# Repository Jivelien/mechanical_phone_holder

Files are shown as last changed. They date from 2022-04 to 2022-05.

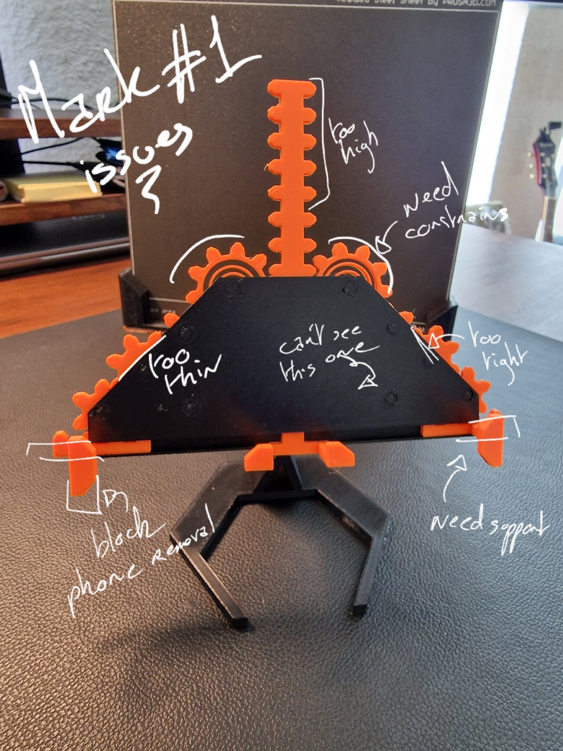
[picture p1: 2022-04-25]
issues_tracing.jpg

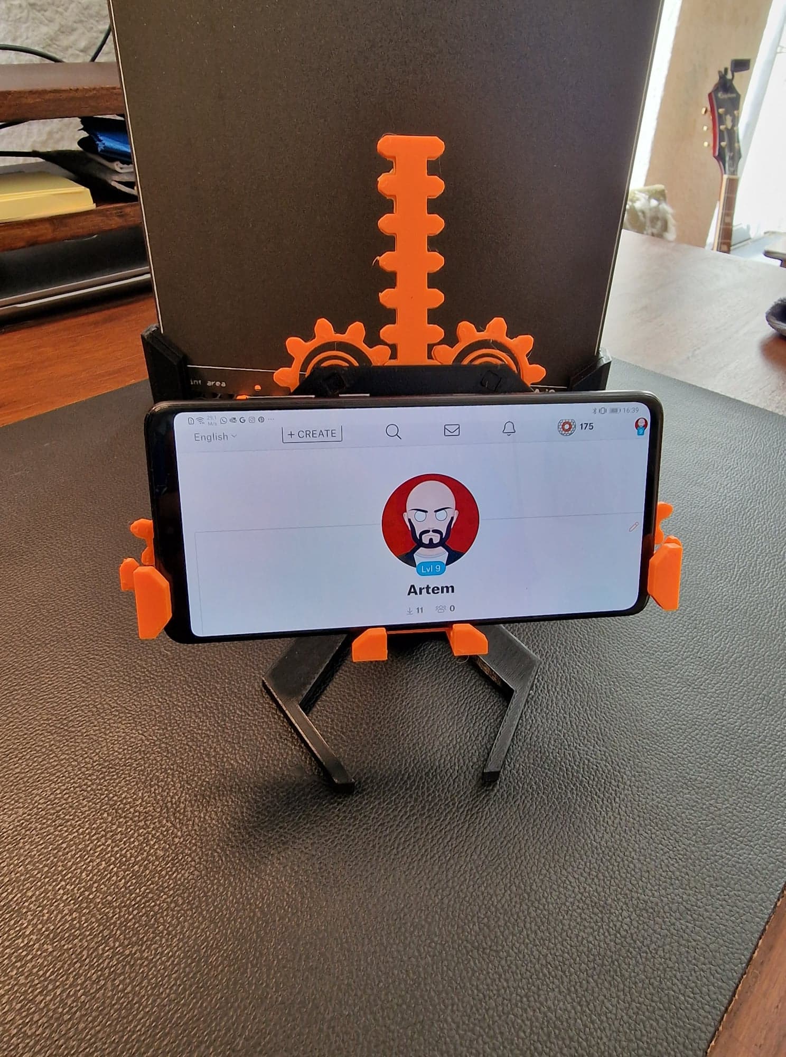
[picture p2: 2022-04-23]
220422-printableSubmission/mk1_horizontal_w_phone.jpg

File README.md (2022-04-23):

# Mechanical phone stand -  Mk 1

This phone gear was design with the constrain to move only using gears (and racks).

This phone holder is suitable for a phone with max dimension of 90x190x19 (a really big phone), and minimal of 60x40x__ (a tamagochi… ¯\_(ツ)_/¯)

When you put your phone on the stand, the vertical rack will move down and leads to all gear moving and grabing your phone from each side.

The top gears contains a spring, which mean that when you take off your phone, it will automatically come back to its default position.

All the design was compute using OpenScad using an homemade gears generator library.

I've learn a lot making this project, and I hope you like it!
Happy printing !

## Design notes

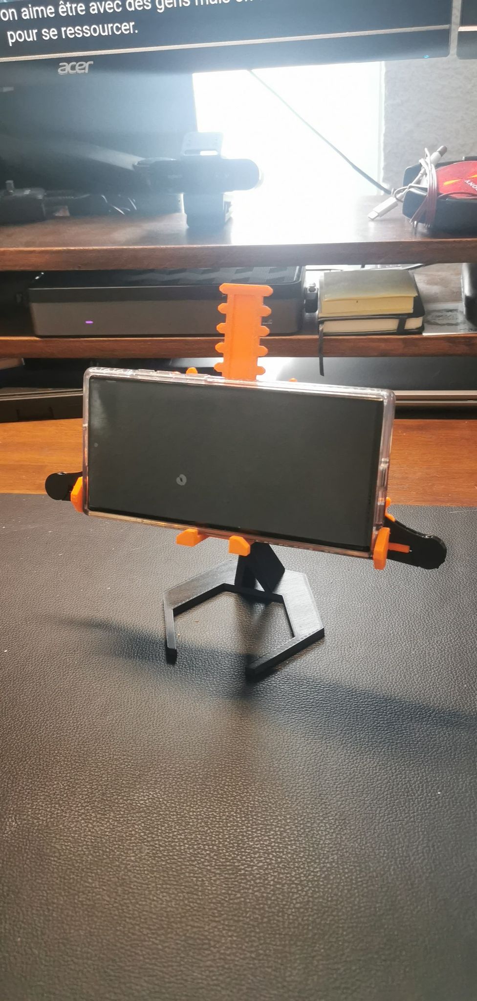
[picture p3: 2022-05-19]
20220519-Mk2_Publish/280579185_324572459750847_7880518313641460600_n.jpg

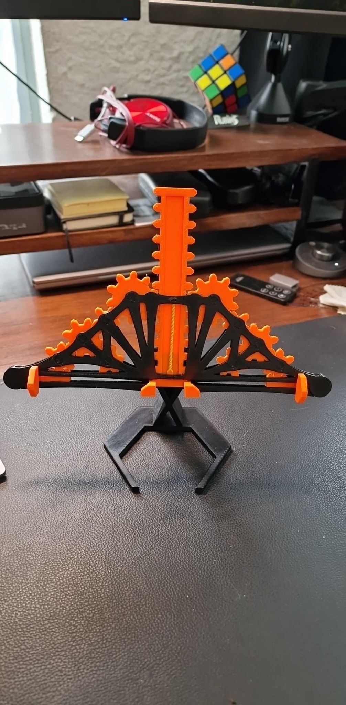
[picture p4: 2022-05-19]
20220519-Mk2_Publish/281888711_434815515040241_3250742157388597709_n.jpg

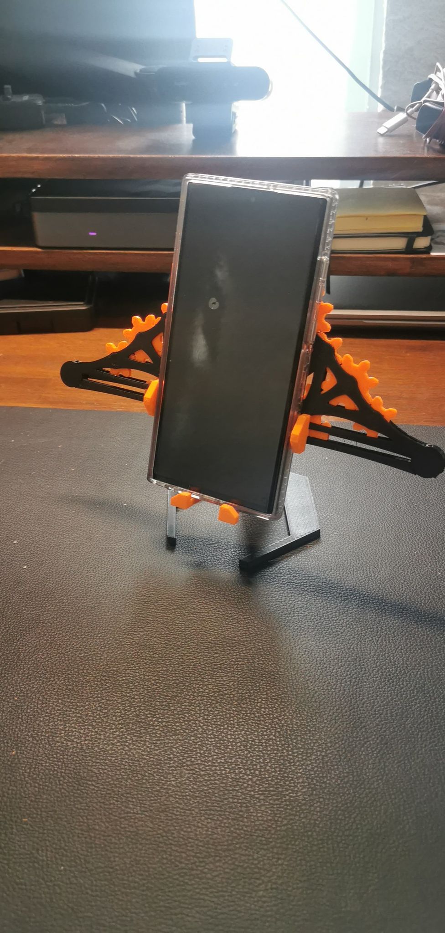
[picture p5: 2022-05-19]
20220519-Mk2_Publish/280890000_410508580699683_3673960678102073021_n.jpg

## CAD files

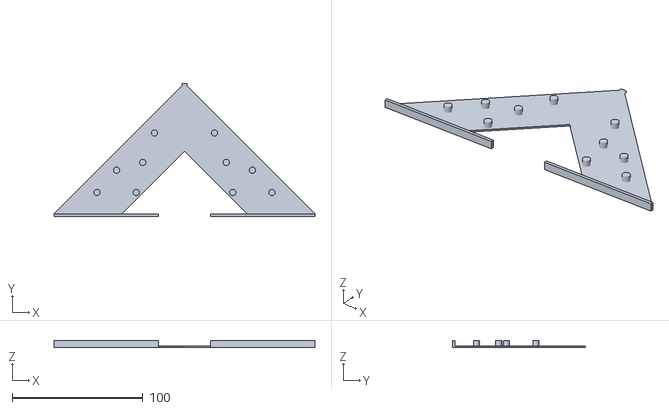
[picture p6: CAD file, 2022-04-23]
20220413-printedPoc/support.stl
200.0 x 102.0 x 5.00

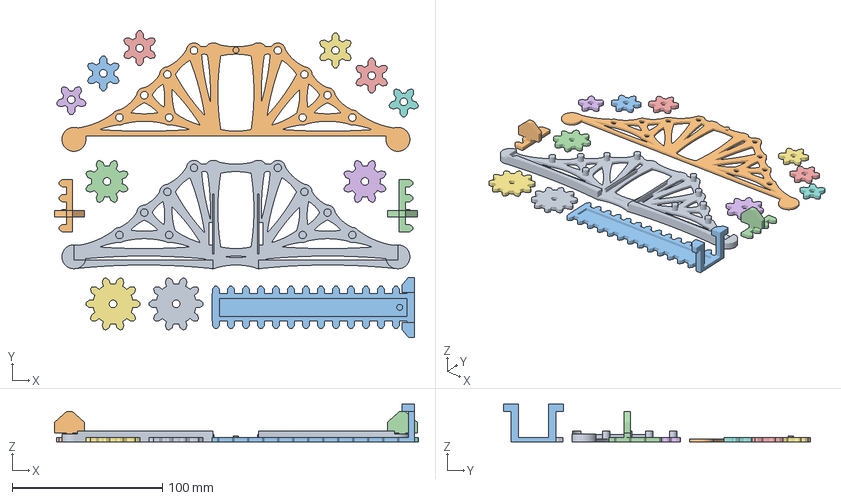
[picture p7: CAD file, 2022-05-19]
20220519-Mk2_Publish/bottom.3mf
242.7 x 204.5 x 25.0 mm
bottom.stl
top.stl
system.stl_1
system.stl_2
system.stl_3
system.stl_4
system.stl_5
system.stl_6
system.stl_7
system.stl_8
system.stl_9
system.stl_10
system.stl_11
system.stl_12
system.stl_13

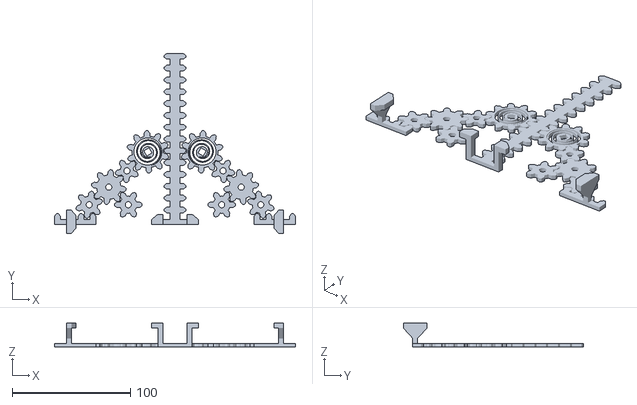
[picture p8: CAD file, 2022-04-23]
220422-printableSubmission/mk1_gears.stl
204.0 x 152.6 x 20.0

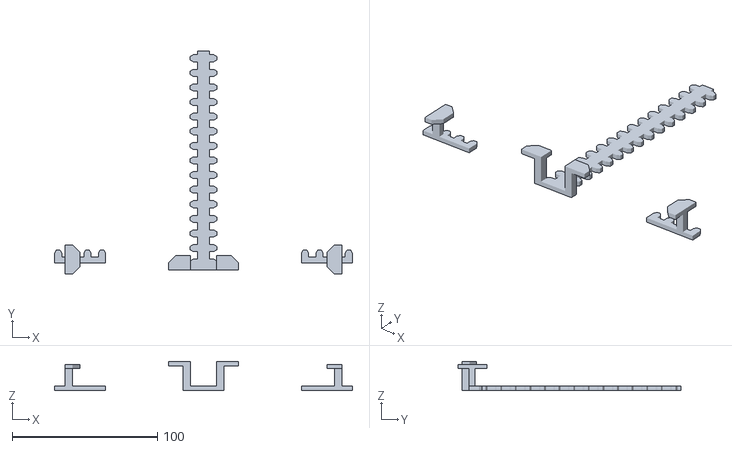
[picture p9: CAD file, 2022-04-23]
20220413-printedPoc/rack.stl
205.1 x 153.5 x 20.0

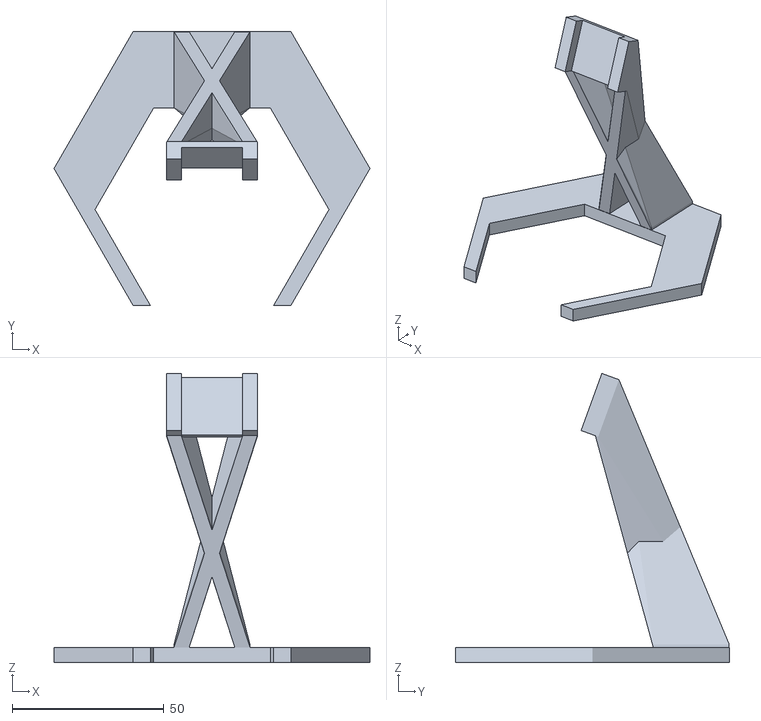
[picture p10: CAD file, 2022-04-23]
220422-printableSubmission/mk1_foot.stl
104.0 x 90.1 x 95.2

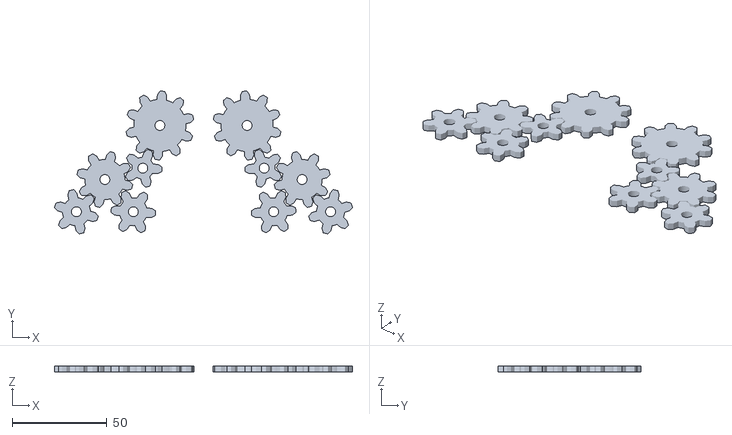
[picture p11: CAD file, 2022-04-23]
20220413-printedPoc/gear.stl
157.1 x 75.3 x 3.00

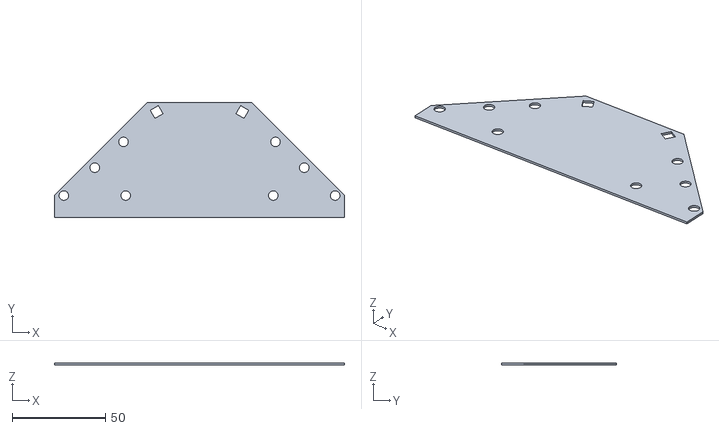
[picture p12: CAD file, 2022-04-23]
220422-printableSubmission/mk1_top_cover.stl
155.2 x 61.4 x 1.00

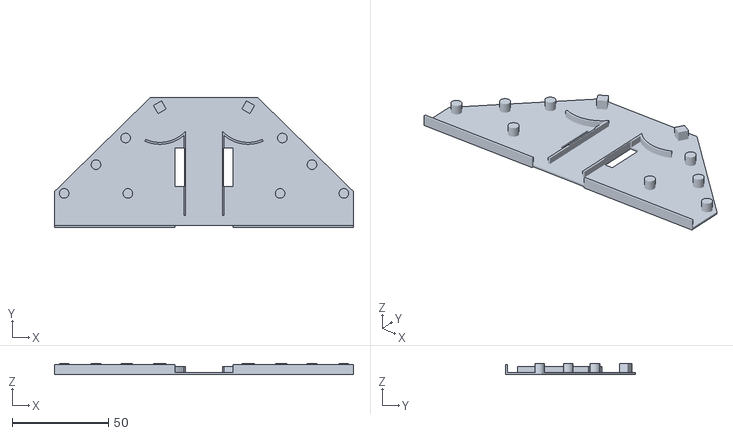
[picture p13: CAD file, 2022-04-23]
220422-printableSubmission/mk1_back.stl
155.2 x 67.4 x 5.50

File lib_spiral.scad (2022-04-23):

module line(point1, point2, width = 1, cap_round = true) {
    angle = 90 - atan((point2[1] - point1[1]) / (point2[0] - point1[0]));
    offset_x = 0.5 * width * cos(angle);
    offset_y = 0.5 * width * sin(angle);

    offset1 = [-offset_x, offset_y];
    offset2 = [offset_x, -offset_y];

    if(cap_round) {
        translate(point1) circle(d = width, $fn = 24);
        translate(point2) circle(d = width, $fn = 24);
    }

    polygon(points=[
        point1 + offset1, point2 + offset1,  
        point2 + offset2, point1 + offset2
    ]);
}

module polyline(points, width = 1) {
    module polyline_inner(points, index) {
        if(index < len(points)) {
            line(points[index - 1], points[index], width);
            polyline_inner(points, index + 1);
        }
    }

    polyline_inner(points, 1);
}

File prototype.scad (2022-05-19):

include <libp_gear.scad>
include <lib_spiral.scad>
include <libp_branch.scad>

toothThickness=5;
toothHeight=5;
thickness =3;
tolerance=0.1;
pin_diameter = 5;
donut_thickness = 0;
hole_diameter = pin_diameter + tolerance;

gear1_numberOfTeeth = 6;
gear2_numberOfTeeth = 8;
gear3_numberOfTeeth = 6;
gear4_numberOfTeeth = 5;
gear5_numberOfTeeth = 10;

centralRack_numberOfTeeth = 14;
sideRack_numberOfTeeth = 4;
sideRackHeight=7;
centralRackHeight=12;
sideRack_translate=11.2;

top_thickness=2;
branch_diameter=5;


pin_height= donut_thickness*2 + top_thickness*2 + tolerance *2 + thickness;

angle_1_2 = 42;
angle_2_3 = -angle_1_2;
angle_2_4 = 180-angle_1_2;
angle_4_5 = 138;

gear1_rotation=0;
gear2_rotation=8;
gear3_rotation=42;
gear4_rotation=-13.5;
gear5_rotation=15;

gear1_x=centralRackHeight+10+getRackLenght(toothThickness, 3)-toothThickness/2;
gear1_y=sideRackHeight+getPitchRadiusFromTeeth(toothThickness, gear1_numberOfTeeth);

gear2_pos = gearPosition(angle_1_2,toothThickness,gear2_numberOfTeeth, gear1_numberOfTeeth, gear1_x, gear1_y);
gear2_x=gear2_pos[0];
gear2_y=gear2_pos[1];

gear3_pos = gearPosition(angle_2_3,toothThickness,gear3_numberOfTeeth, gear2_numberOfTeeth, gear2_x, gear2_y);
gear3_x=gear3_pos[0];
gear3_y=gear3_pos[1];

gear4_pos = gearPosition(angle_2_4,toothThickness,gear4_numberOfTeeth, gear2_numberOfTeeth, gear2_x, gear2_y);
gear4_x=gear4_pos[0];
gear4_y=gear4_pos[1];

gear5_pos = gearPosition(angle_4_5,toothThickness,gear5_numberOfTeeth, gear4_numberOfTeeth, gear4_x, gear4_y);
gear5_x=gear5_pos[0];
gear5_y=gear5_pos[1];

support_border = 1.5;

spacingGear_Border = tolerance *2;
gear5_fullRadius = getFullRadiusFromTeeth(toothThickness, gear5_numberOfTeeth, toothHeight);
gear4_fullRadius = getFullRadiusFromTeeth(toothThickness, gear4_numberOfTeeth, toothHeight);
gear3_fullRadius = getFullRadiusFromTeeth(toothThickness, gear3_numberOfTeeth, toothHeight);
gear2_fullRadius = getFullRadiusFromTeeth(toothThickness, gear2_numberOfTeeth, toothHeight);
gear1_fullRadius = getFullRadiusFromTeeth(toothThickness, gear1_numberOfTeeth, toothHeight);


gear5_pitchRadius = getPitchRadiusFromTeeth(toothThickness, gear5_numberOfTeeth);
gear4_pitchRadius = getPitchRadiusFromTeeth(toothThickness, gear4_numberOfTeeth);
gear3_pitchRadius = getPitchRadiusFromTeeth(toothThickness, gear3_numberOfTeeth);
gear2_pitchRadius = getPitchRadiusFromTeeth(toothThickness, gear2_numberOfTeeth);
gear1_pitchRadius = getPitchRadiusFromTeeth(toothThickness, gear1_numberOfTeeth);


module gearPoc(numberOfTeeth) {
    color("#FF4500")
        difference() {
            gear(toothThickness,numberOfTeeth,toothHeight,thickness,tolerance);
            translate([0,0,2]) cylinder(thickness+2, d=hole_diameter, $fn=100, center = true);
        }
}

module SideRack(){
    a=getSolidrackWidth(sideRackHeight, toothHeight);
    color("#FF4500") {
        rack(toothThickness, sideRack_numberOfTeeth, toothHeight, sideRackHeight, thickness, tolerance);
        translate([0,10,0]) {
            cube([a,a,20]);
            hull() {
                translate([0/2,0,20-a]) cube(a);
                #translate([-(20-a)/2,0,10-a]) cube([20,a,a+3]);
                }   
            }
        }
}

module spring_pin() {
    cylinder(2,r1=1, r2=2);
}

module CentralRack() {
    module LeftHalfCentralRack() {
        difference(){
                rack(toothThickness, centralRack_numberOfTeeth, toothHeight, centralRackHeight, thickness, tolerance);
            translate ([0,5,1]) cube([centralRackHeight/2,centralRack_numberOfTeeth*5*2-15,thickness +1 ]);
            }
            translate([0,10,1]) spring_pin();
            
            
            cube([10,5,thickness]); 
            translate([10,0,0]){
                cube([5,getSolidrackWidth(sideRackHeight,toothHeight),20]);
                hull() {
                    translate([0,0,20]) cube([10,getSolidrackWidth(sideRackHeight,toothHeight),5]);
                    translate([0,4.2,20]) cube([5,4.2,5]);
                }
           }
    }
    color("#FF4500") {
        union() {
            LeftHalfCentralRack();
            mirror([1,0,0]) LeftHalfCentralRack();
            
        }
    }
}

/*
Contour();
mirror([1,0,0]) Contour();
*/
module branch_set(circle_diameter,thickness=thickness,bottom=true) {
    translate([gear1_x,gear1_y,0]) 
        rotate([0,0,angle_1_2]) 
            branch(circle_diameter,gear1_pitchRadius+gear2_pitchRadius,thickness);
    
    translate([gear2_x,gear2_y,0]) 
        rotate([0,0,angle_2_3]) 
            branch(circle_diameter,  gear2_pitchRadius+gear3_pitchRadius,thickness);
    
    translate([gear2_x,gear2_y,0]) 
        rotate([0,0,angle_2_4])
            branch(circle_diameter,gear2_pitchRadius+gear4_pitchRadius,thickness);
    
    translate([gear4_x,gear4_y,0]) 
        rotate([0,0,angle_4_5])
            branch(circle_diameter,gear4_pitchRadius+gear5_pitchRadius,thickness);
    
    distance_1_4= sqrt((gear1_x-gear4_x)^2+(gear1_y-gear4_y)^2);
    angle_1_4=angle_1_2-angle_2_4-176;
    translate([gear1_x,gear1_y,0]) 
        rotate([0,0,angle_1_4]) 
            branch(circle_diameter,distance_1_4,thickness);
    
    distance_1_3= sqrt((gear1_x-gear3_x)^2+(gear1_y-gear3_y)^2);
    translate([gear1_x,gear1_y,0]) 
        branch(circle_diameter,distance_1_3,thickness);
    
    branch_3_out_x = getRackLenght(toothThickness, sideRack_translate) ;
    branch_3_out_y = sideRackHeight/2 ;
    distance_3_border= sqrt((branch_3_out_x-gear3_x)^2+(branch_3_out_y-gear3_y)^2);
    translate([gear3_x,gear3_y,0]) 
        rotate([0,0,-22])  
            branch(circle_diameter,distance_3_border,thickness);
    
    bottom_branch_x=centralRackHeight+toothHeight/2;
    bottom_branch_y=5;
    bottom_branch_lenght=branch_3_out_x-bottom_branch_x+1;
    translate([bottom_branch_x,bottom_branch_y,0])
        branch(circle_diameter,bottom_branch_lenght,thickness);
    if (bottom) {
        translate([bottom_branch_x+bottom_branch_lenght,2,0]) cylinder(thickness, r=8);
        difference() {
        translate([bottom_branch_x,bottom_branch_y-6,0])
            branch(circle_diameter,bottom_branch_lenght,thickness+5.2);
       
        translate([bottom_branch_x+bottom_branch_lenght,2,0]) difference() {
            cylinder(thickness+5.4, r=8.1);
            translate([-16,-18.2,0]) cube(16);
            }
            
        translate([bottom_branch_x+bottom_branch_lenght,2,thickness+3+donut_thickness+tolerance]) cylinder(thickness+5.4, r=8.1);
        a=200;
        translate([-a/2,-tolerance,-0.5]) cube([a+2,getSolidrackWidth(sideRackHeight,toothHeight)+tolerance*2,thickness+6]);
       
        translate([0,-10,0]) cube(15.2); 
            
       }
    }
    translate([bottom_branch_x+bottom_branch_lenght,2,0]) cylinder(thickness, r=8);
    
    distance_1_corner= sqrt((bottom_branch_x-gear1_x)^2+(bottom_branch_y-gear1_y)^2);
    translate([bottom_branch_x,bottom_branch_y,0])
        rotate([0,0,21])
            branch(circle_diameter,distance_1_corner,thickness);
    
    distance_5_corner= sqrt((bottom_branch_x-gear5_x)^2+(bottom_branch_y-gear5_y)^2);
    translate([bottom_branch_x,bottom_branch_y,0])
        rotate([0,0,76.5])
            branch(circle_diameter,distance_5_corner,thickness);
    
    distance_4_corner= sqrt((bottom_branch_x-gear4_x)^2+(bottom_branch_y-gear4_y)^2);
    translate([bottom_branch_x,bottom_branch_y,0])
        rotate([0,0,52])
            branch(circle_diameter,distance_4_corner,thickness);
    
    distance_5_upcorner= sqrt((bottom_branch_x-gear5_x)^2+(gear5_y-gear5_y)^2);
    translate([bottom_branch_x,gear5_y,0])
        rotate([0,0,0])
            branch(circle_diameter,distance_5_upcorner,thickness);
    
    distance_corners= sqrt((bottom_branch_x-bottom_branch_x)^2+(bottom_branch_y-gear5_y)^2);
    translate([bottom_branch_x,bottom_branch_y,0])
        rotate([0,0,90])
            branch(circle_diameter,distance_corners,thickness);
}
        
module half_system(circle_diameter,thickness=thickness) {
    difference() {
        union() {
            translate([gear1_x,gear1_y,-donut_thickness]) donut(branch_diameter,pin_diameter/2,donut_thickness);
            translate([gear2_x,gear2_y,-donut_thickness]) donut(branch_diameter,pin_diameter/2,donut_thickness);
            translate([gear3_x,gear3_y,-donut_thickness]) donut(branch_diameter,pin_diameter/2,donut_thickness);
            translate([gear4_x,gear4_y,-donut_thickness]) donut(branch_diameter,pin_diameter/2,donut_thickness);
            translate([gear5_x,gear5_y,-donut_thickness]) donut(branch_diameter,pin_diameter/2,donut_thickness);
            branch_set(circle_diameter,thickness=thickness, bottom=false);
                }
                    
    translate([gear1_x,gear1_y,-donut_thickness-1]) cylinder(thickness+2,r=pin_diameter/2);
    translate([gear2_x,gear2_y,-donut_thickness-1]) cylinder(thickness+2,r=pin_diameter/2);
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

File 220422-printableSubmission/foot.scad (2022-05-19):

translate([15.55,10.05,-4]) cube([2.4,14.9,6.5]);
translate([-15.45-2.5,10.05,-4]) cube([2.4,14.9,6.5]);
translate([-(15.55+15.45+2.5+2.5)/2,10.05,-4.2]) cube([15.55+15.45+2.5+2.5,14.9,2]);

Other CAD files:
220422-printableSubmission/libp_branch.scad
20220413-printedPoc/lib_rack_and_gear.scad
20220413-printedPoc/poc.scad
220422-printableSubmission/libp_gear.scad

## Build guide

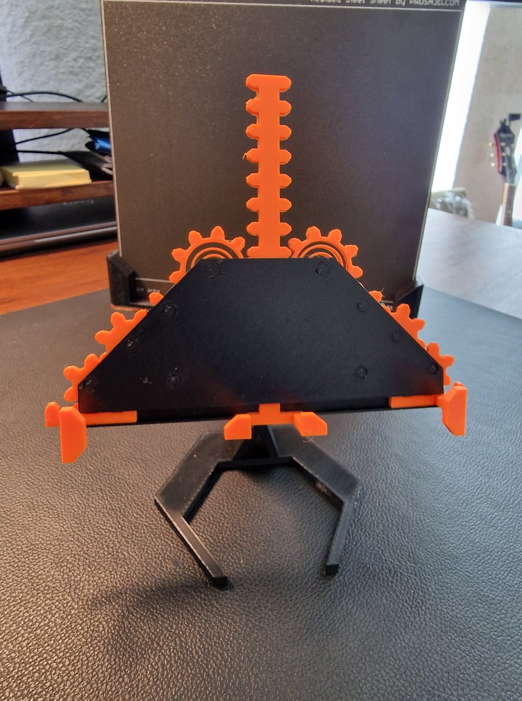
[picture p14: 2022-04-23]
220422-printableSubmission/mk1_stand_wo_phone.jpg

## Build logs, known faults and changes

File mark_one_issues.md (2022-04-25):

# Mark I issue

 - Central rack is too high : Two to three tooth can't be remove from the central rack, for smaller design purpose

 - Spring gears don't hold in place : Spring gear are not constrained in top, driving to some "tooth jumping" when phone is removed from the support. 

 - Top and Bottom plate are too close : they are not spaced enought to allow free rotation of the gears

 - Side rack are loosy : they are on cantilever when the support is in default position, driving it to fall sometimes

 - Side rack interfere with phone removal

 - Front and bottom plate are too thin and don't allow a good fixation

 - Front and bottom plate aren't see though so some gear are not visible at all

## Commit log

2022-04-25 Printable context submission
    [poc.scad, prototype.scad, prototype_without_bord.scad]
2022-05-12 add branch module
    [libp_branch.scad, prototype.scad]
2022-05-12 add first layer of surface
    [prototype.scad]
2022-05-17 continue holding and add spring in central rack
    [flat_springV1_3.scad, libp_branch.scad, libp_gear.scad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]
2022-05-19 trying with flat spring but not working
    [foot.scad, prototype.scad]
2022-05-19 main frame done
    [prototype.scad]
2022-05-19 add submission to printable
    [bottom.3mf, flat_springV1_3.scad, foot.scad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]
